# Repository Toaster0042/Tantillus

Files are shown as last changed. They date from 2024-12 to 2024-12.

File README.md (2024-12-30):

# Tantillus
My remix of the tantillus, a cross gantry printer from 2012. 
This version uses a frame printed in a single piece, a mosquito/NF Crazy and Vz Hextrudort on top to bring it to a more recent standard. 
The fishing lines have also been swapped over to GT2 Belts for better quality and uses a 2:1 gear ratio on the stepper to the motion components. <br>
The travel is about 108mm on X, 109mm on Y and 143mm on Z, printable volume is about 100x100x140mm.<br>
<br>
The body of the printer requires a 207x200x295mm print so beware before starting this project, the short version only requires a 207x200x250mm printer but the Z axis travel is reduced to 100mm.

Assembly Video:

IMAGE ALT TEXT (https://www.youtube.com/watch?v=rofUXSk4k1Y "Tantillus Assembly")

## BOM

[Excel BOM](https://github.com/Toaster0042/Tantillus/blob/main/BOM.xlsx)<br>
[Github BOM](BOM.md)<br>

## Contact  

@Glizzynator. on discord
<br>

## Credits

<br>

-PCB for the breakout board by [Lhndo](https://github.com/lhndo/LH-Stinger/tree/main/PCB/LHS%20Breakbeat)<br>
-Original Tantillus by [Intrinsically-Sublime](https://reprap.org/wiki/Tantillus)<br>
-VZ hextrudort by [the vzbot team](https://github.com/VzBoT3D/Vz-HextrudORT)<br>
-Side blowers by Cbon123<br>
<br>

## License

This work is licensed under a [Creative Commons (4.0 International License)  ](https://creativecommons.org/licenses/by-nc-sa/4.0/)  
[**Attribution—Noncommercial—Share Alike**](LICENSE.md)  
<br>
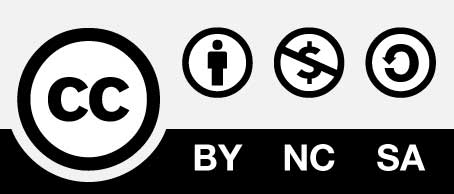
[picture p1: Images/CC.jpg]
  
<br>

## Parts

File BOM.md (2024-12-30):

# Tantillus BOM
You will need to cut the 8mm shafts to length <br>
Many parts can be bought for cheaper since all the parts here are rather quality ones, the sourcing is aproximate and can change with sales and price modifications

#### Required Hardware
| Item | Qty | Price per | Price total | link |
| --- | --- | --- | --- | --- |
| 2a 0.9 stepper | 2 | 32 | 64 | [https://sparta3d.ca/products/ldo-42sth48-2004mahvrn](https://sparta3d.ca/products/ldo-42sth48-2004mahvrn) |
| V0 leadscrew motor | 1 | 30 | 30 | https://www.omc-stepperonline.com/us-on-sale-nema-17-external-34mm-stack-0-4a-lead-8mm-0-31496-length-200mm-us-17ls13-0404e-200g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 |
| Nema 14 extruder motor | 1 | 20.5 | 20.5 | [https://www.omc-stepperonline.com/round-nema-14-bipolar-0-9deg-9-ncm-12-75-oz-in-1-0a-%CF%8636x17-5mm-4-wires-14hr07-1004vrn](https://www.omc-stepperonline.com/round-nema-14-bipolar-0-9deg-9-ncm-12-75-oz-in-1-0a-%CF%8636x17-5mm-4-wires-14hr07-1004vrn) |
| 230mm 8mm shaft | 6 | 8 | 48 | [https://www.aliexpress.com/item/32885378366.html](https://www.aliexpress.com/item/32885378366.html) |
| 200mm 6mm shaft | 2 | 6.29 | 12.58 | [https://www.aliexpress.com/item/32905232067.html](https://www.aliexpress.com/item/32905232067.html) |
| vzhextrudort | 1 | 72.38 | 72.38 | [https://www.aliexpress.com/item/1005004574888848.html](https://www.aliexpress.com/item/1005004574888848.html) |
| Nf-crazy | 1 | 41 | 41 | Message Mellow on aliexpress |
| Berd air pump | 1 | 18 | 18 | [https://www.aliexpress.com/item/1005002755232729.html](https://www.aliexpress.com/item/1005002755232729.html) |
| Barbed fitting | 1 | 11.2 | 11.2 | https://www.mcmaster.com/3913N75/ |
| LM6UU | 2 | 0.679 | 6.79 | [https://www.aliexpress.com/item/32913566642.html](https://www.aliexpress.com/item/32913566642.html) |
| LM8UU | 4 | 3.345 | 13.38 | https://vi.aliexpress.com/item/4001122539243.html |
| LM8LUU | 2 | 3.965 | 7.93 | [https://www.aliexpress.com/item/32880760873.html](https://www.aliexpress.com/item/32880760873.html) |
| 608 bearings | 8 | 3.938 | 39.38 | [https://www.aliexpress.com/item/1005004988198954.html](https://www.aliexpress.com/item/1005004988198954.html) |
| 6mm GT2 20T pulley 5mm bore | 2 | 4.395 | 8.79 | [https://www.aliexpress.com/item/33002989677.html](https://www.aliexpress.com/item/33002989677.html) |
| 6mm GT2 20T pulley 8mm bore | 8 | 3.8225 | 30.58 | [https://www.aliexpress.com/item/4001116400764.html](https://www.aliexpress.com/item/4001116400764.html) |
| 6mm GT2 40T pulley 8mm bore | 2 | 8.395 | 16.79 | [https://www.aliexpress.com/item/1005003549557428.html](https://www.aliexpress.com/item/1005003549557428.html) |
| 6mm Closed loop GT2 180mm belt | 2 | 2.75 | 5.5 | [https://sparta3d.ca/products/gt2-timing-belt-l-98mm-w-6mm-2gt-closed-loop-synchronous-belt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](https://sparta3d.ca/products/gt2-timing-belt-l-98mm-w-6mm-2gt-closed-loop-synchronous-belt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) |
| 6mm GT2 belt 4m | 1 | 14 | 14 | https://sparta3d.ca/products/gt2-timing-belt?_pos=1&_sid=2ac400e73&_ss=r |
| 6x3mm magnets | 14  | 0.2205 | 4.41 | [https://www.aliexpress.com/item/1005006769269318.html](https://www.aliexpress.com/item/1005006769269318.html) |
| 5x25mm shaft | 2 | 0.3275 | 6.55 | [https://vi.aliexpress.com/item/1005004157086244.html](https://vi.aliexpress.com/item/1005004157086244.html) |
| 4.5x15x0.5mm spring | 2 | 0.1965 | 3.93 | [https://vi.aliexpress.com/item/1005005312536098.html](https://vi.aliexpress.com/item/1005005312536098.html) |
| Silicone Spacers (12mm) | 1 | 1.2475 | 4.99 | [https://vi.aliexpress.com/item/1005007994881592.html](https://vi.aliexpress.com/item/1005007994881592.html) |
| Igus E2 mircro series 3 (1ft) | 1 | 19.53 | 19.53 | [https://www.igus.ca/product/series-03?artnr=03-05-028-0](https://www.igus.ca/product/series-03?artnr=03-05-028-0) |
| KFB0612HAFDB | 2 | 20 | 40 | [https://www.mouser.ca/ProductDetail/Delta-Electronics/KFB0612HAFDB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](https://www.mouser.ca/ProductDetail/Delta-Electronics/KFB0612HAFDB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) |
| CNC Bed Frame (6061 alu) | 1 | 61 | 61 | [https://www.pcbway.com/rapid-prototyping/manufacture/?type=1&reffercode=TOP](https://www.pcbway.com/rapid-prototyping/manufacture/?type=1&reffercode=TOP) |
| CNC'd bed (5083 cast alu or equivalent) | 1 | 61 | 61 | [https://www.pcbway.com/rapid-prototyping/manufacture/?type=1&reffercode=TOP](https://www.pcbway.com/rapid-prototyping/manufacture/?type=1&reffercode=TOP) |
| Bed Heater | 1 | 40 | 40 | [https://keenovo.store/collections/custom-keenovo-silicone-heaters/products/keenovo-custom-designed-and-manufactured-silicone-heaters-payment-link](https://keenovo.store/collections/custom-keenovo-silicone-heaters/products/keenovo-custom-designed-and-manufactured-silicone-heaters-payment-link) |
| Electronics | 1 | 0 | 0 | Chose your own |
| total ($CAD) | | | 702.21 | |
| total without bed | | | 540.21 | |

<br>

| Fasteners | QTY |
| --- | --- |
| DIN 7991 M2x5 | 2 |
| ISO 4762 M2 x 6 | 2 |
| M2.5x25 SHCS | 2 |
| DIN 4762 M3x8 SHCS | 101 |
| DIN 7991 M3x8 Countersunk  | 4 |
| DIN 4762 M3x10 SHCS | 27  |
| DIN 4762 M3x20 SHCS | 3 |
| ISO 7380 M3x25 BHCS | 2 |
| DIN 934 M3 Hex Nut | 4 |
| ISO 7089 M3 Washer | 103 |
| 8mm Shim Washer 1mm | 8 |
| M2 Heatset Insert | 1 |
| M2.5 Heatset Insert | 2 |
| M3 Heatset Insert | 112 |
| M3x8 Standoff | 5 |
| DIN 472 12x1 Retainer Ring | 2 |
| DIN 472 15x1 Retainer Ring | 4 |

[README](README.md)

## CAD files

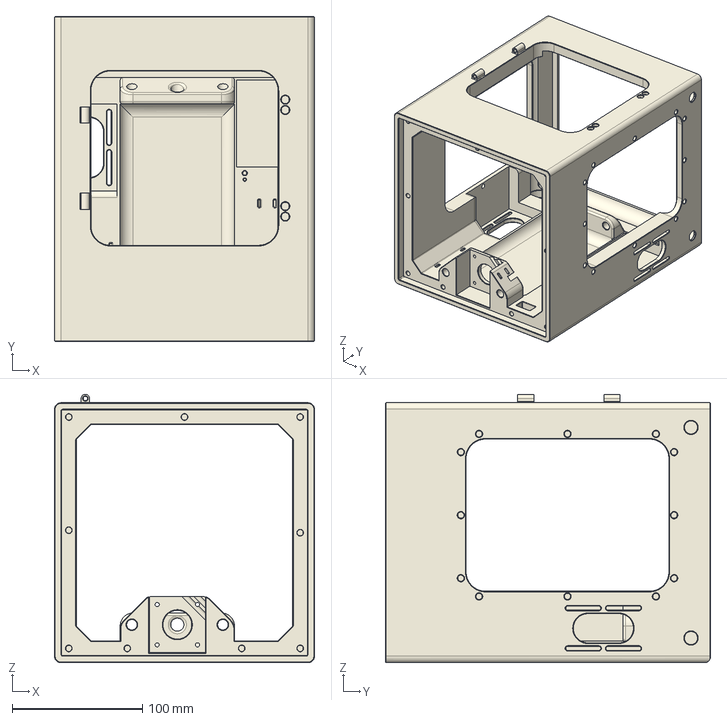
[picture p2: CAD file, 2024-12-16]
Short_Tantillus.step
200.0 x 250.0 x 206.5 mm

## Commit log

2024-11-23 Update Tantillus.step
    Updated to the latest revision of the assembly
2024-12-15 Tantillus REV1
    First revision of the final assembly, everything should be in order but it has not been assembled yet
2024-12-16 Added the short version
    Added the short version of the frame that is 250mm tall
    [Short_Tantillus.step]
2024-12-16 Update README.md
    added credit for the breakout pcb
2024-12-30 BOM
    Added the BOM and fixed some fasteners and the LGX extruder in the assembly
    [BOM.xlsx]
2024-12-30 Create BOM.md
    adding a BOM.md file
